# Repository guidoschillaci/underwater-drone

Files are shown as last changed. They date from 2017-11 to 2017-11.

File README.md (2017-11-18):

# A customisable underwater robot
This repository contains the open source 3D-printable models for a customisable underwater drone. The work and the models are described in the following arXiv publication:

Schillaci, G., Schillaci, F. and Hafner, V.V. A Customisable Underwater Robot, arXiv preprint arXiv:1707.06564. 2017. Link to the paper: <a href="https://arxiv.org/abs/1707.06564" target="_blank">https://arxiv.org/abs/1707.06564 </a>

For any feedback, please contact us:

<a href="https://adapt.informatik.hu-berlin.de/schillaci/" target="_blank">Guido Schillaci</a>: guido.schillaci at informatik.hu-berlin.de

<a href="http://www.schillaci.org/" target="_blank">Fabio Schillaci</a>: fabio at schillaci.org

See license and disclaimer information below.

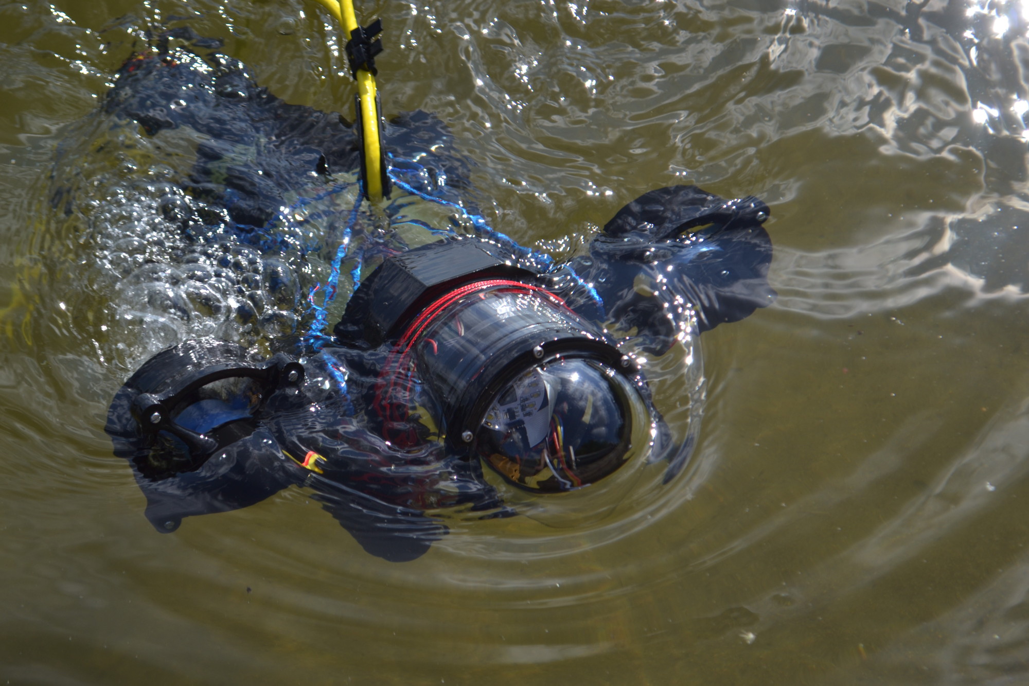
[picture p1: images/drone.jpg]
Drone


# Instructions

The models provided here allows for multiple propeller and ballast configurations. They are compatible with the 4" watertight enclosure sold by <a href="https://www.bluerobotics.com/">BlueRobotics</a>. 

The 3D model files (step and igs) and 3D printable files (.stl) of each component can be found in the Models folder. 

It is recommended to 3D print the objects with solid infill. 

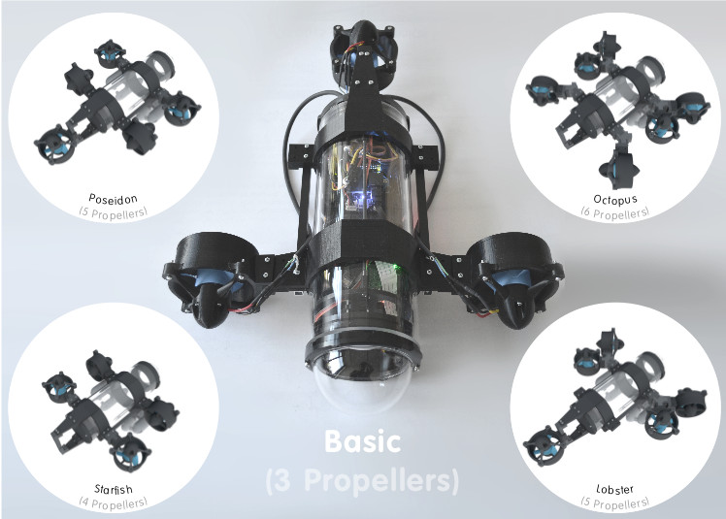
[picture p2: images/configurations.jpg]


## Thrusters
Thrusters (inspired on BlueRobotics thrusters) are compatible with Turnigy Aerodrive DST brushless motors (tested DST-700 and DST-1200, so far). Please note that the models provided here are not compatible with the M100 and M200 motors sold by BlueRobotics.

The following figures illustrate a mounted propeller and an exploded version showing its components.

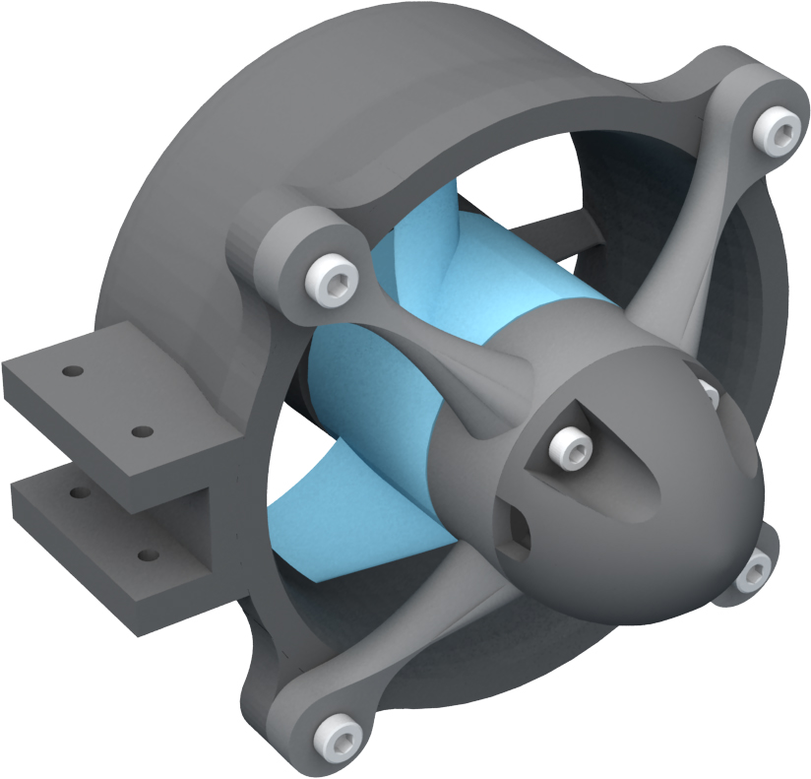
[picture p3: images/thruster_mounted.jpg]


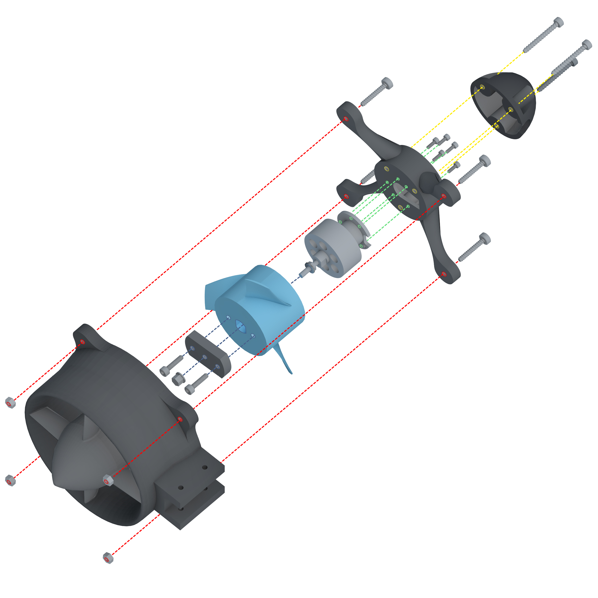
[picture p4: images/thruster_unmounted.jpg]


The objects are named in the Models folder as follows. Starting from the bottom left object (not considering nuts and bolts):

* thruster_main (.igs, .stp, .stl)

* propeller_dst_2_bluerov_adapter (.igs, .stp, .stl)

* propeller (.igs, .stp, .stl): the propeller is a modification of the original T200 propeller developed by BlueRobotics, which can be ordered from Bluerobotics' store. The version provided here fits better with Turnigy DST motors.

* motor: the figure illustrate a Turnigy DST-700. Model is not provided here

* thruster_motor_mount (.igs, .stp, .stl): the motor is mounted onto this X shaped component. The thruster_motor_mount is then mounted onto the thurster_main component. This mount has holes aligned with those of DST motors bases. It has not been tested yet with Bluerobotics M100 or M200 motors, so it may be not compatible.

* thruster_cap.stl (.igs, .stp, .stl)

## Clamps and posterior support

Two sets of clamps have been designed that allow easy customisation of thrusters and ballast configurations.

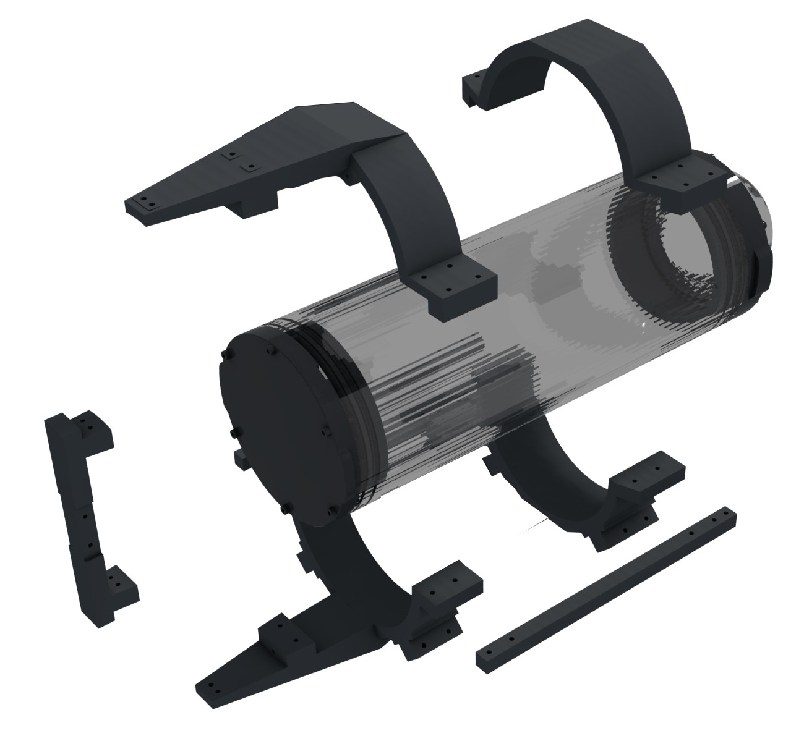
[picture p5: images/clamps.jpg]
clamps


The model files are named as follows

* clamp_anterior_superior (.igs, .stp, .stl): the upper part of the anterior clamp. It has two mounting points (left and right) for motors, ballasts or adapters.

* clamp_anterior_inferior (.igs, .stp, .stl): the lower part of the anterior clamp. It has two mounting points (+45 degrees, -45 degrees) for motors, ballasts or adapters.

* stick (.igs, .stp, .stl): this stick can be screwed to both the posterior and anterior lower clamps. 

* clamp_posterior_superior (.igs, .stp, .stl): the upper part of the posterior clamp. It has two mounting points (left and right) for motors, ballasts or adapters. It has an additional structure for mounting the support for rear motors or ballasts. 

* clamp_posterior_inferior (.igs, .stp, .stl): the lower part of the posterior clamp. It has two mounting points (+45 degrees, -45 degrees) for motors, ballasts or adapters. It has an additional structure for mounting the support for rear motors or ballasts.

* rear_clamp_connector (.igs, .stp, .stl): it connects the two posterios clamps and provides an additional mounting point for a motor, ballast or adapter.

* posterior_clamp_2_tube_connector (.igs, .stp, .stl): this small elements allows to screw the posterior clamps (the same can be used for both the upper and lower parts) into the cap of the Bluerobotics watertight enclosure.

## Mounting points

Clamps and rear connector have several mounting points for motors, ballasts and adapters. 

For instance, a motor can be plugged onto a mounting point of the anterior clamp as in the following illustration:

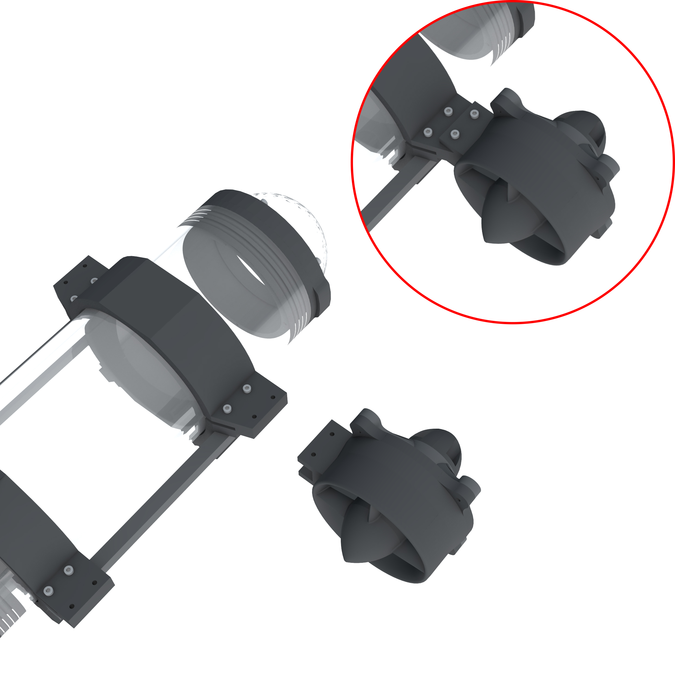
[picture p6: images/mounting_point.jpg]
mounting_point


We designed three adapters to allow rotating the original mounting point.

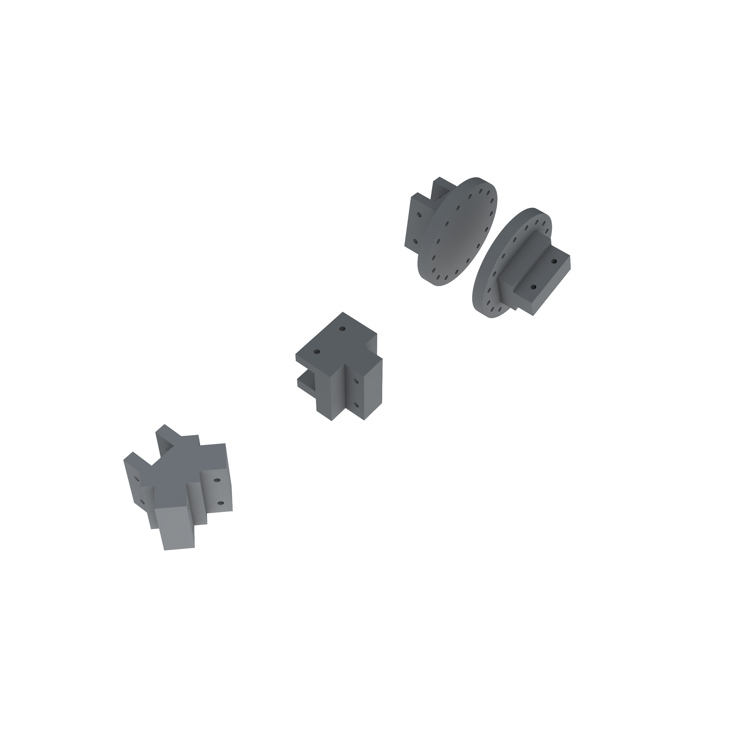
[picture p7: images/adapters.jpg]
adapters


* adapter_90 (.igs, .stp, .stl): allows rotating the original mounting point of 90 degrees. It can be used, for instance, to mount a vertical thruster, as in the following illustration:

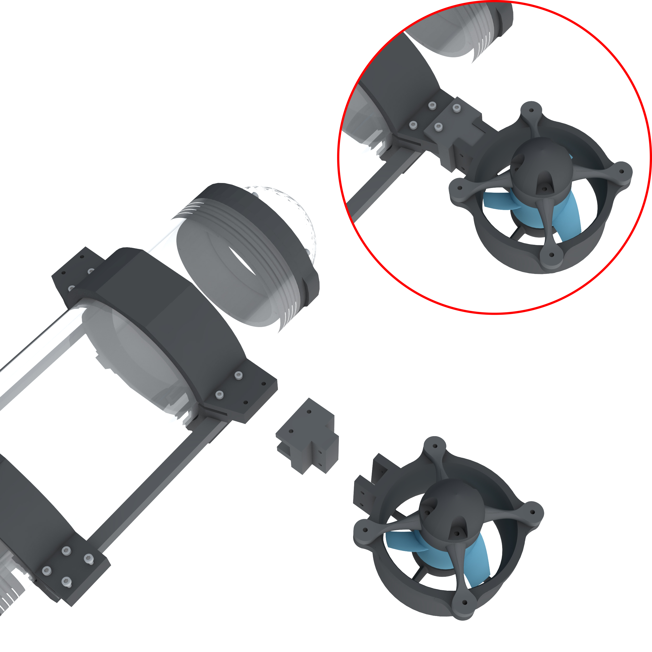
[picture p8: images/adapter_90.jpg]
adapter 90


* adapter_round[_male, _female] (.igs, .stp, .stl): allows 5 different rotation angles within 90 degrees. It can be used, for instance, to mount a diagonal thruster, as in the following illustration:

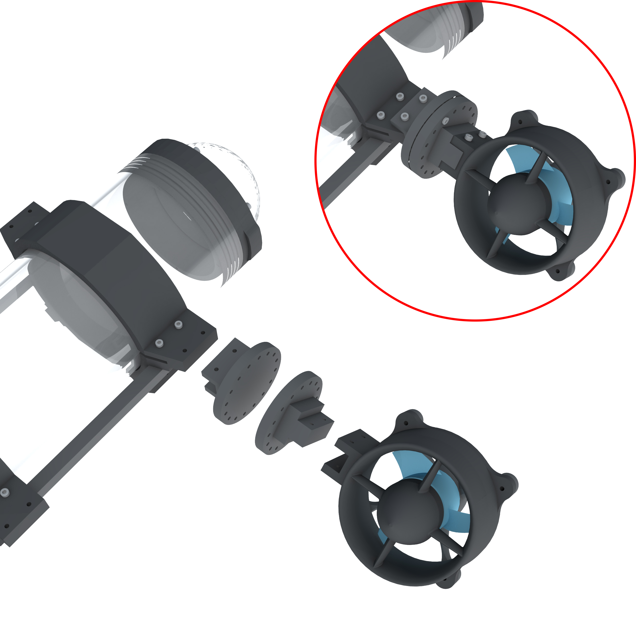
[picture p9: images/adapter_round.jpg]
adapter round


* adapter_split (.igs, .stp, .stl): splits a mounting point into two, rotated at +45 and -45 degrees in respect to the original mounting point orientation. A combination of this and the previous adapters allows for a great number of possible thruster configurations, as in the example illustrated in the following figure.

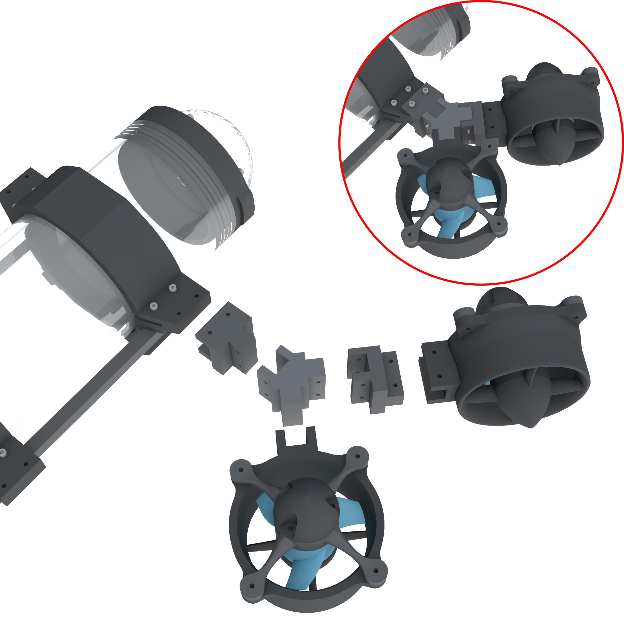
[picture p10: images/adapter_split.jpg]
adapter split


## Ballast

We designed a ballast structure with mounting points compatibles with those described above. The structure is a cylinder that can be filled with ballast, such as stainless steel balls (we used 10mm steel ball; each ballast cylinder filled with these balls weighted around 300-400 grams).

The ballast structure is composed by a cylinder and two caps:

* ballast_cylinder (.igs, .stp, .stl): it has two separate compartments that can be filled to better set the center of mass of the drone. It has a mounting point that fits with those of the clamps and adapters

* ballast_cap (.igs, .stp, .stl): two caps have to be printed to close the cylinder on both sides.

# License and disclaimer
<br />The work and the models provided here have been created by Fabio Schillaci and Guido Schillaci and are licensed under a <a rel="license" href="http://creativecommons.org/licenses/by/4.0/">Creative Commons Attribution 4.0 International License</a>.

In no case shall the authors of this work be liable for any injury, loss, claim, or any direct, indirect, incidental, punitive, special, or consequential damages of any kind, including, without limitation lost profits, lost revenue, lost savings, loss of data, replacement costs, or any similar damages, whether based in contract, tort (including negligence), strict liability or otherwise, arising from your use of any of the models and the material provided here, or for any other claim related in any way to your use of the models and the material provided here, including, but not limited to, any errors or omissions in any content, or any loss or damage of any kind incurred as a result of the use of the models and the material provided. Because some states or jurisdictions do not allow the exclusion or the limitation of liability for consequential or incidental damages, in such states or jurisdictions, our liability shall be limited to the maximum extent permitted by law.

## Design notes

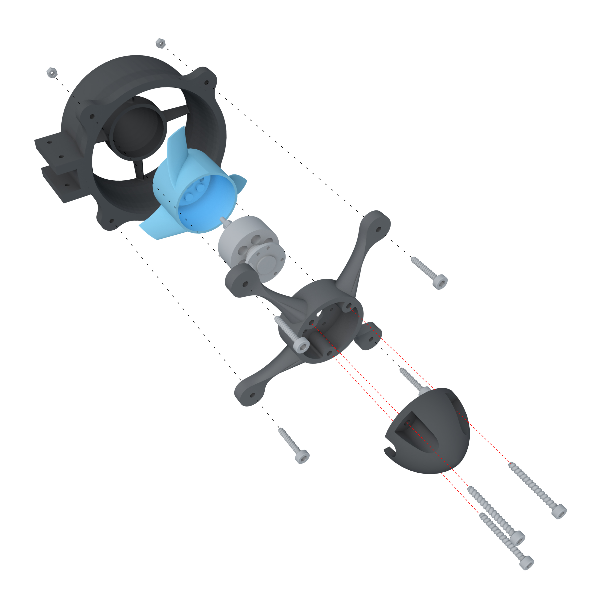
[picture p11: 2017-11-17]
images/thruster_unmounted_2.jpg

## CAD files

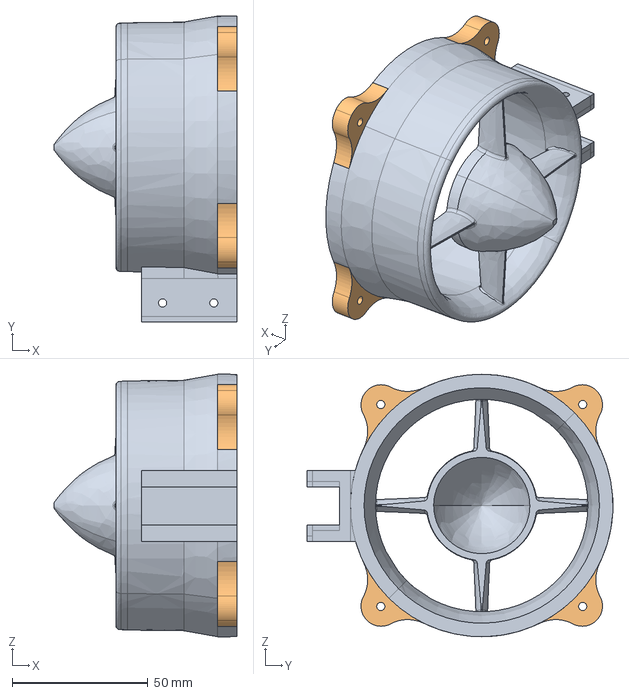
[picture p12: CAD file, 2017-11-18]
models/thruster_main.stp
67.2 x 112.6 x 96.6 mm

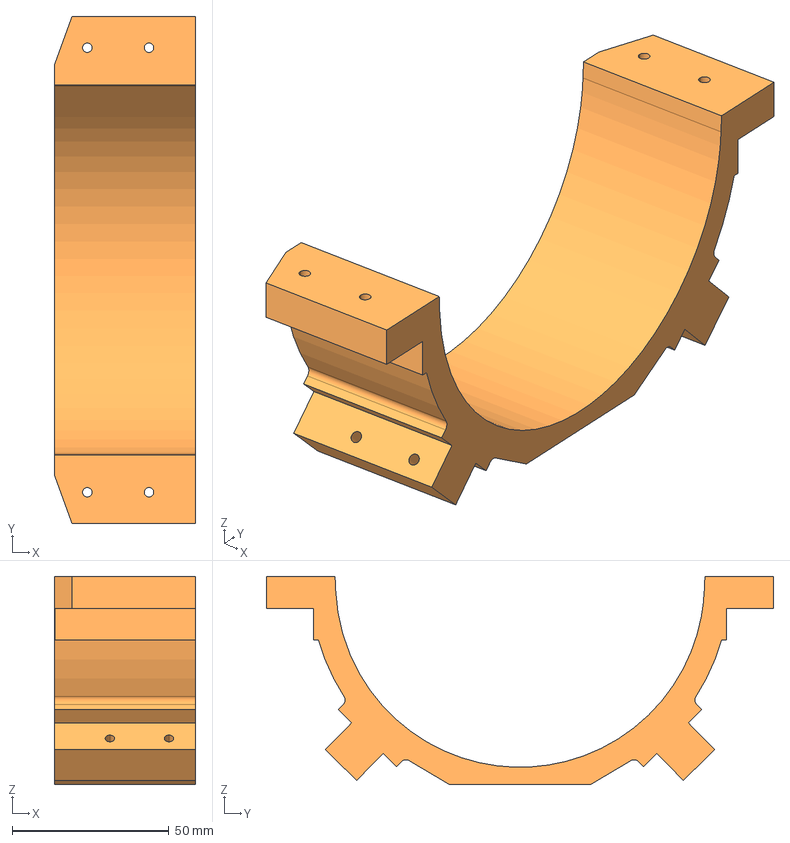
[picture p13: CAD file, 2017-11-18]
models/clamp_anterior_inferior.stp
45.0 x 161.6 x 66.2 mm

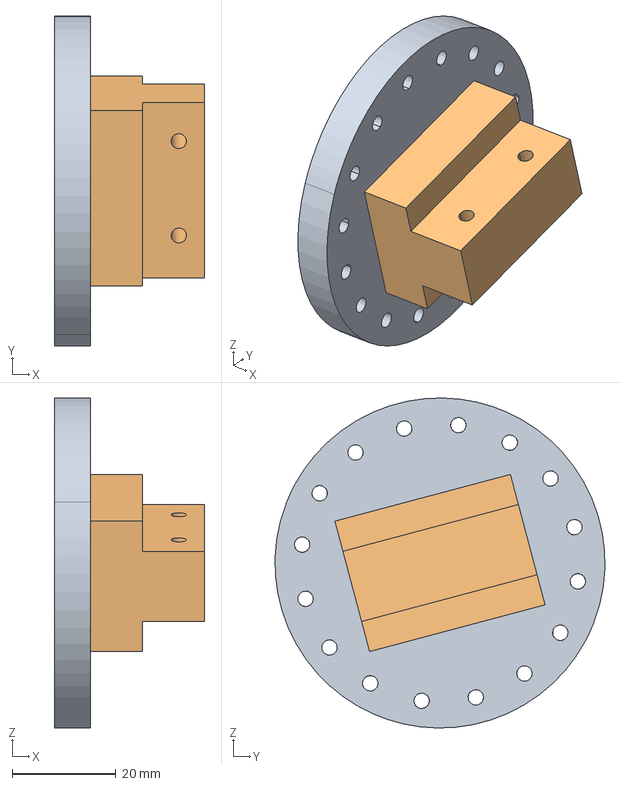
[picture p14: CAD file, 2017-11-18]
models/adapter_round_male.stp
29.0 x 63.6 x 63.6 mm

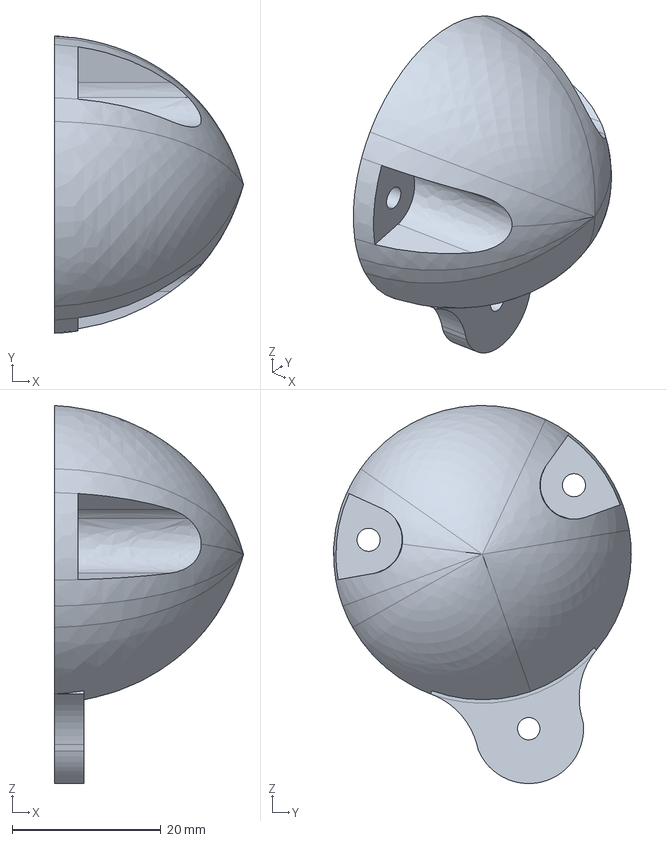
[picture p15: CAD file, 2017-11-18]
models/ballast_cap.stp
25.4 x 40.0 x 50.8 mm

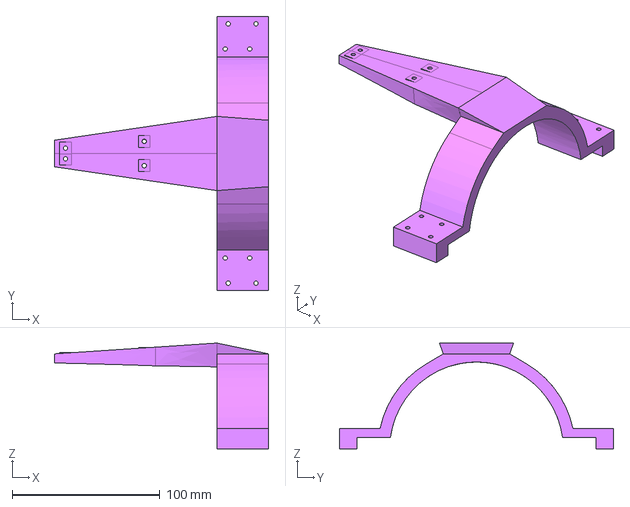
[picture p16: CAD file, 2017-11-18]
models/clamp_posterior_superior.stp
145.0 x 185.6 x 71.7 mm

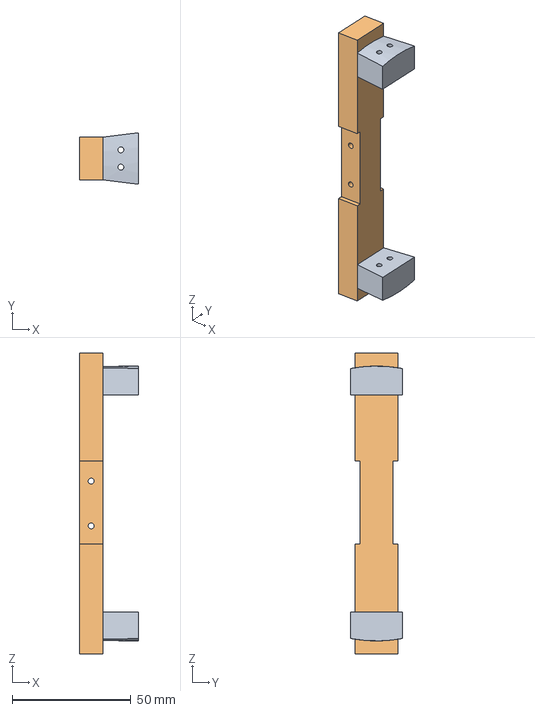
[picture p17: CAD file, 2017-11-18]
models/rear_clamp_connector.stp
25.0 x 21.7 x 126.5 mm

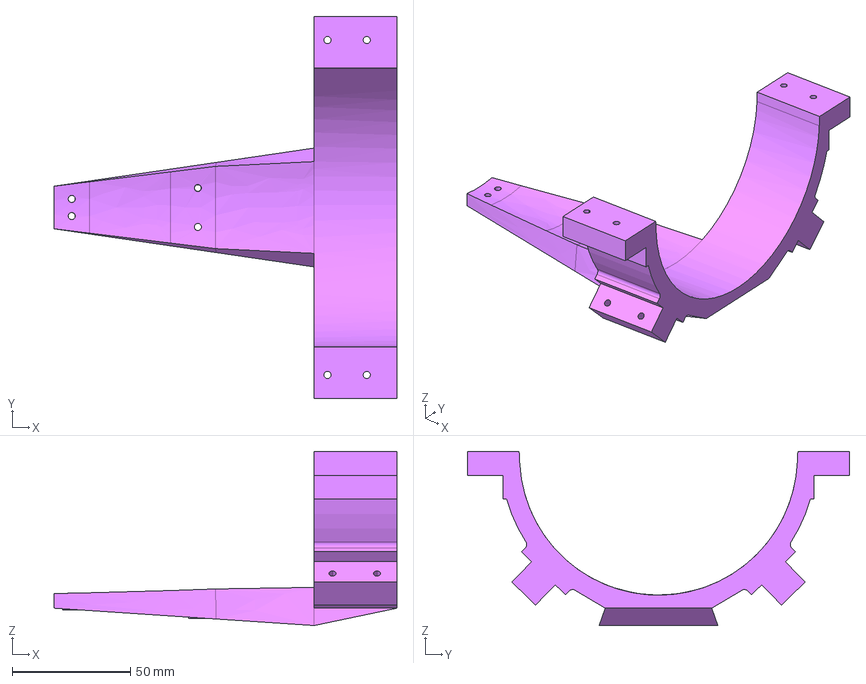
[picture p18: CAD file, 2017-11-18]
models/clamp_posterior_inferior.stp
145.0 x 161.6 x 73.6 mm

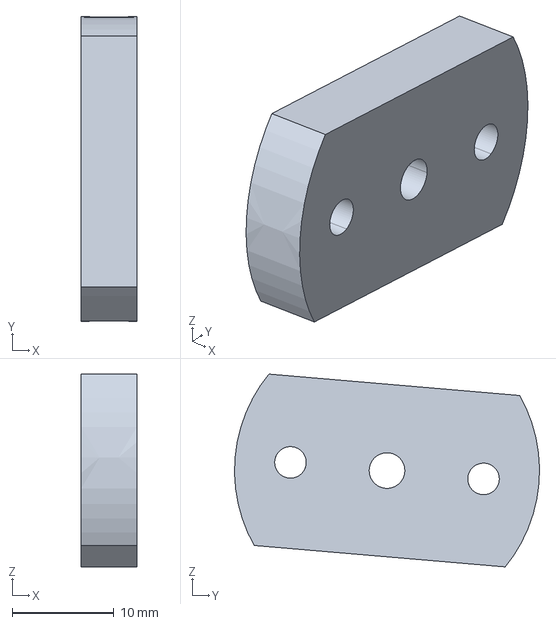
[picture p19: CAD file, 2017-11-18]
models/thruster_dst_2_bluerov_adapter.stp
5.50 x 30.0 x 19.0 mm

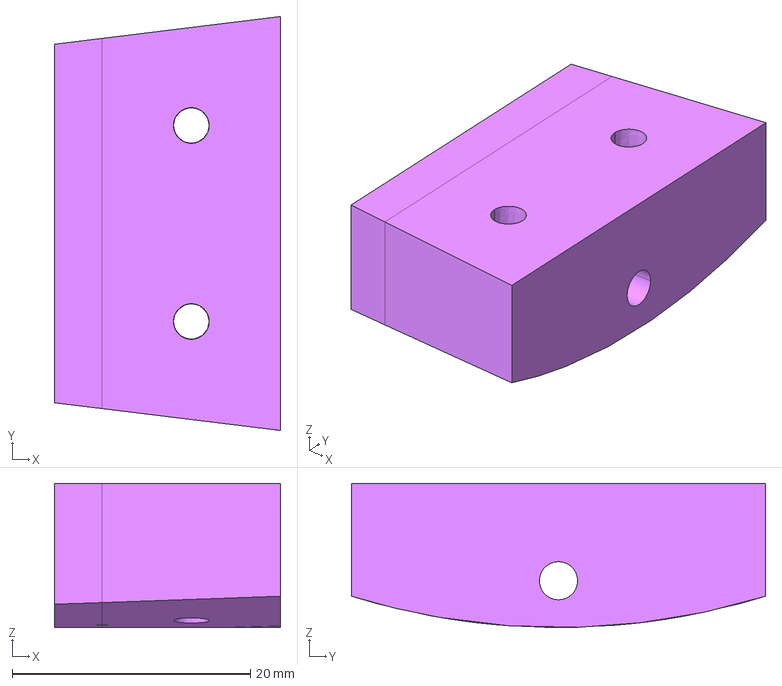
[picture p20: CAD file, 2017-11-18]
models/posterior_clamp_2_tube_connector.stp
19.0 x 34.8 x 12.1 mm

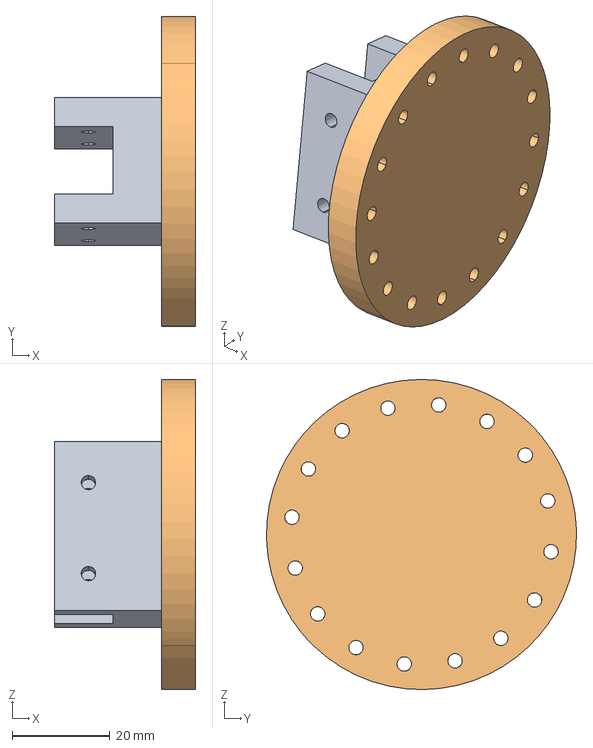
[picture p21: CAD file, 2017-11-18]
models/adapter_round_female.stp
29.0 x 63.6 x 63.6 mm

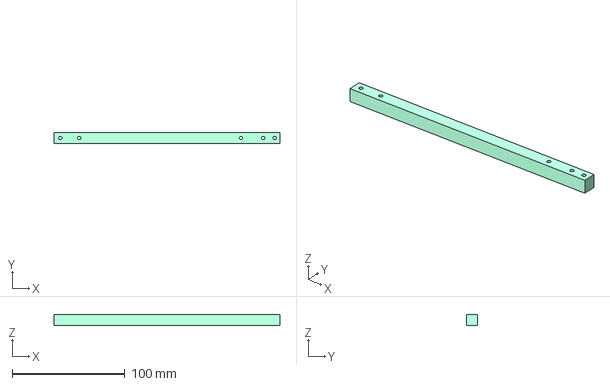
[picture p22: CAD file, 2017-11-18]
models/stick.igs
200.0 x 10.0 x 10.0 mm

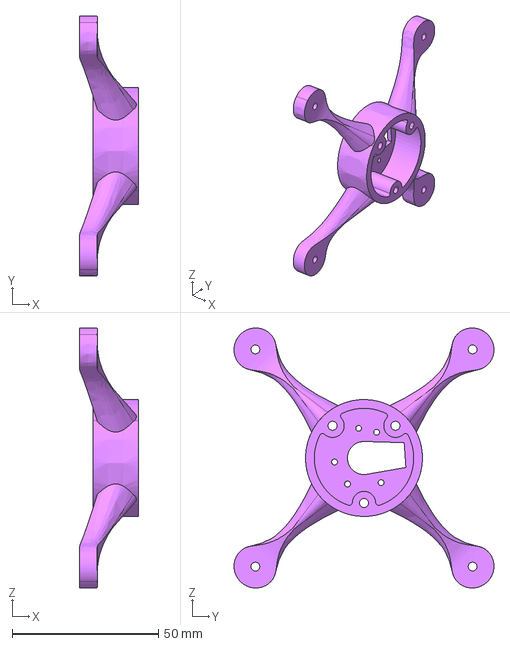
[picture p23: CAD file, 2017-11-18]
models/thruster_motor_mount.stp
20.0 x 88.9 x 88.9 mm

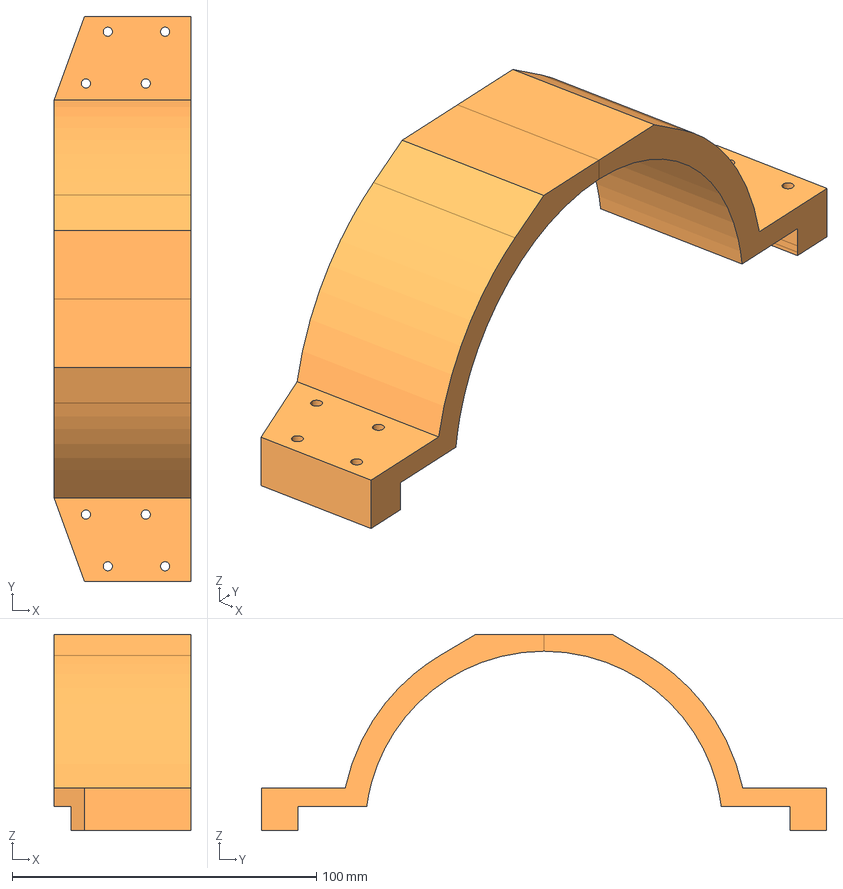
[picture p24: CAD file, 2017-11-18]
models/clamp_anterior_superior.stp
45.0 x 185.6 x 64.4 mm

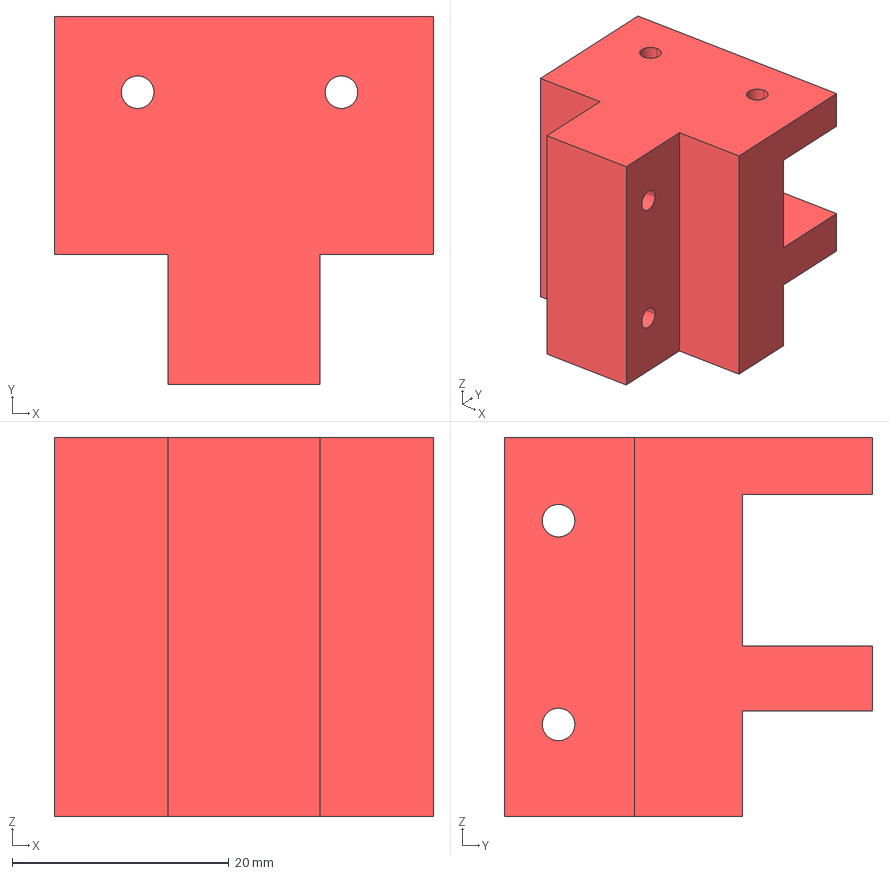
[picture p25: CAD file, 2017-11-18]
models/adapter_90.stp
35.0 x 34.0 x 35.0 mm

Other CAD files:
models/propeller.stp
models/adapter_split.stp
models/ballast_cylinder.stp
models/thruster_cap.stp
models/adapter_90.igs
models/adapter_90.stl
models/adapter_round_female.igs
models/adapter_round_female.stl
models/adapter_round_male.igs
models/adapter_round_male.stl
models/adapter_split.igs
models/adapter_split.stl
models/ballast_cap.igs
models/ballast_cap.stl
models/ballast_cylinder.igs
models/ballast_cylinder.stl
models/clamp_anterior_inferior.igs
models/clamp_anterior_inferior.stl
models/clamp_anterior_superior.igs
models/clamp_anterior_superior.stl
models/clamp_posterior_inferior.igs
models/clamp_posterior_inferior.stl
models/clamp_posterior_superior.igs
models/clamp_posterior_superior.stl
models/posterior_clamp_2_tube_connector.igs
models/posterior_clamp_2_tube_connector.stl
models/propeller.igs
models/propeller.stl
models/rear_clamp_connector.igs
models/rear_clamp_connector.stl
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

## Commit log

2017-11-17 adapter models
    [adapter_90.stl, adapter_round_femal.stl, adapter_round_male.stl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]
2017-11-17 thrusters description and models
    [propeller.stl, thruster_cap.stl, thruster_dst_2_bluerov_adapter.stl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]
2017-11-17 changes in readme and in models
    [thruster_dst_2_bluerov_adapter.stl]
2017-11-18 added models
    [adapter_90.igs, adapter_90.stl, adapter_90.stp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]
2017-11-18 more info
    [posterior_clamp_2_tube_connector.igs, posterior_clamp_2_tube_connector.stl, posterior_clamp_2_tube_connector.stp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]
